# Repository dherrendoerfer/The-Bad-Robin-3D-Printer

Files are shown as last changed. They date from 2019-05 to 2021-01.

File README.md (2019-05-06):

# The Bad Robin 3D Printer
The Bad Robin 3D Printer is an Open-Source 3D Printer project. Its goal is to provide an 
affortable, versatile and robust 3D Printer design.  
It was designed for the use in schools and universities, where the availablility of spare parts are key to the success
of a 3D Printer, and so it was designed to be able to produce its own spare parts. Also a school printer should be easy to store,
so this frame design was chosen to use as little shelf space as possible .  

### Main design features
- It is built-up of only well-established parts that are widely available.
- It features a new single-fan extruder desing for a super-light extruder with print cooling.
- It is parametric: Height, width or length may change, the 3D-Printed parts that make it up always remain the same.
- It is rugged: The base and frame are very strong if the printer ever becomes un-aligned it is very easy to fix.
- It provides superior quality prints: The desing is made to minimise vibrations and wobble making for great prints.
- It can replicate: Even the smallest (250mm) variant can print all the parts for its larger siblings.
- It is affordable: Depending on sourcing, the price does not exceed $250 for the 250mm version. 
- It is expandable: Multicolor or Heated printbed ? Everything is possible.

Licensed under GPL:
## The Bad Robin 3D printer project files
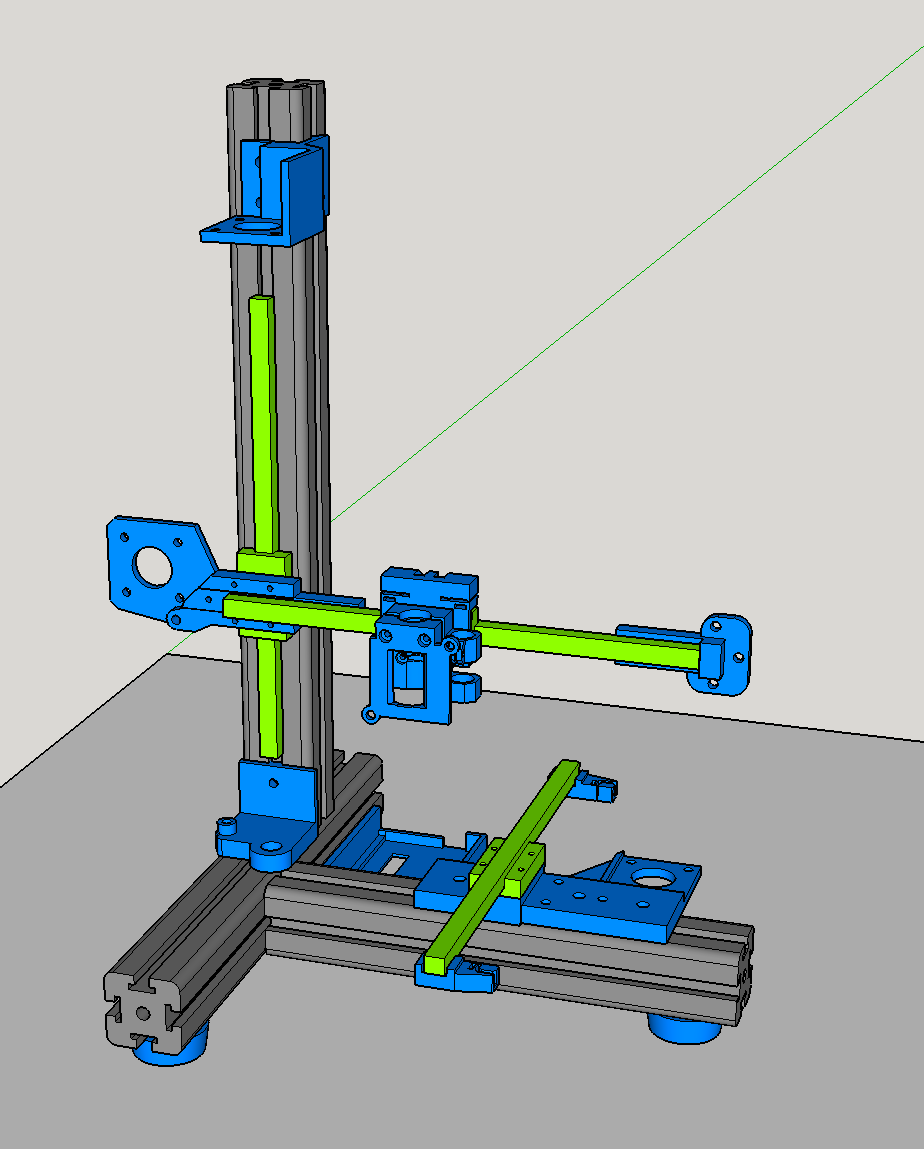
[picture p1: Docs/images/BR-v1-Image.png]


For more information see the Bill-of-materials and the documentation in the Docs directory.

## Videos:
The development of the 3D Printer and its beginnings are documented on my YouTube Channel.  

The general intro video is here:  
https://www.youtube.com/watch?v=5juObRKD8EM&list=PLotvT33qzzfLR7SWEICwr2An6o4muybxc

There is a build video available here:  
https://www.youtube.com/watch?v=sfIAuq82kME&list=PLotvT33qzzfLR7SWEICwr2An6o4muybxc

And don't forget:  
    have FUN!  
D.Herrendoerfer

Donations:  
If you would like to make a donation to keep this project and others going you can do so at:  
https://www.paypal.me/dherrendoerfer  
This helps a lot !

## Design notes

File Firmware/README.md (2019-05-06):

### Firmware files for the Bad Robin 3D printer
This folder includes the required files for building the firmware for the Bad Robin
3D printer. Note that these files may be out-of-sync with the official version of Repetier.

The official Repetier firmware can be found here: https://www.repetier.com/documentation/repetier-firmware/

Repetier is licensed under the GNU GENERAL PUBLIC LICENSE (v3). A copy of the license can be found in the
same directory as this file. Make sure to read and understand it before sharing anything contained here.

The version of Repetier in the Repetier directory contains software addons required for the operation and
safety of the Bad Robin Printer. Do not operate the 3D printer without porting these changes forward.

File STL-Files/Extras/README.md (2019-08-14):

This folder contains things that are strictly speaking not needed for the bare printer, but might help the interrested to get it looking or working neater.

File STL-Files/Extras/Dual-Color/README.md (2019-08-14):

## Multi Meaterial Mod Files
These files are for a modification to support dual material/color print 
Note that the tubes inside the Y-mixer need to be lined with PTFE tube, and the end of the joining (single) tube should be opened up with a drill to help with the insertion of the filament. 
All the connections should be made with locking PTFE clamps, make sure not to overtighten them.

The firmware for the dual color mod and the tool-change scripts are not freely available yet, please contact me for a copy if you can't get it to work yourself. 

###This is still Work-In-Progress

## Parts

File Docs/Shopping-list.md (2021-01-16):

##Shopping list (Date: Feb. 2020):

- ITEM Profile:

https://www.ebay.de/itm/ALU-Profil-Aluprofil-40x40-Nut-8-Aluminium-Profil-AlClipTec/261818937804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

- Bearings:

https://www.ebay.de/itm/20-Kugellager-685-2RS-5-x-11-x-5-mm/251275830725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

- TR8 Nut:

https://www.ebay.de/itm/Trapezgewindemutter-ESKM-8x1-5-rechts-Stahl-Sechskant-SW15L12/273422712592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

or

https://www.ebay.de/itm/Trapezgewindemutter-ESKM-MS-8X1-5-rechts-Rotguss-Sechskant-SW17L15/273700033030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

- TR8 Rod: 

https://www.ebay.de/itm/Prazisions-Trapezgewindespindel-RPTS-TR-8X1-5-rechts-C35-C45-50cm/273177877971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

- Profile Nuts (8mm) 

* You need M3, M5, and M6

https://www.ebay.de/itm/Aluprofil-Profil-10x-Nutensteine-T-Nut-M5-Nut-8/380187272689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

https://www.ebay.de/itm/Aluprofil-Profil-10x-Nutensteine-mit-Kugel-Nut-8/262643806083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

* This type for the M3:

https://www.ebay.de/itm/Nutensteine-schwer-fur-40er-45er-Aluprofile-Stahl-Nut-8-10-M3-M4-M5-M6-M8/132371894755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

- Linear Rail:

https://www.amazon.de/gp/product/B07LDBNVTW  

- Proximity Switch:

https://www.amazon.de/gp/product/B071ZQ6VV6/ref=oh_aui_detailpage_o01_s00?ie=UTF8&psc=1

- Hot-End:

https://www.amazon.de/YOTINO-Extruder-Drucker-Makerbot-Messing/dp/B078SLDBY3/ref=sr_1_5_sspa

- Fan:

https://www.amazon.de/gp/product/B06XZR6VQV/ref=oh_aui_detailpage_o03_s00?ie=UTF8&psc=1

- Extruder Driver: ( Order the 3-Pieces set !)

https://www.amazon.de/TEVO-Titan-Extruder-Komplettpaket-17-Schrittmotor-Bowdenzug-Befestigungsschellen/dp/B073YMY6CP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

- Steppers:

https://www.ebay.de/itm/Longs-Motor-stepping-motor-17HS4401N-nema17-57oz-for-3D-Printer-Reprap-DE-Ship/202105774039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

- RAMPS Kit:

http://bit.ly/3rPzlYX
or (if available):
https://www.amazon.de/Controller-Schrittmotor-Treiber-Heatsink-Grafik-Smart-Display-Controller-3D-Drucker/dp/B01NCZ09Q5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

- Belt & Pulley

https://www.amazon.de/MOHOO-Zahnriemen-Riemenscheibe-Bohrung-Drucker/dp/B01AU3LRRG/ref=sr_1_2_sspa

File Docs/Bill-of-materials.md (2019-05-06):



### All files and information provided here is licensed under the GNU PUBLIC LICENSE 
Make sure you understand the license requirements and implications before moving on.

### Design decision:
The Z-Axis can be held in place by a 3D-printed part and a ball-bearing ball, or a different 3D-printed part and a bearing. For this mounting method the threaded rod needs to be machined to fit the bearing. (Items that this influences are marked with *)

### Bill of materials

- You need each and every stl file printed once, the feet 3 times.
- You need T-Nuts with M3, M5, and M6 screws in various sizes and lengths.
- You need a drill-press to drill two holes

Please also consult the file:
https://github.com/dherrendoerfer/The-Bad-Robin-3D-Printer/blob/master/Docs/Shopping-list.md 
for hints on what to get.

#### You need to source:
- 3x MGN12H linear rails with 250mm length 
- 1x ITEM 40mm aluminium profile 400mm long
- 1x ITEM 40mm aluminium profile 300mm long
- 1x ITEM 40mm aluminium profile 250mm long
- 3x Stepper motors NEMA17 bipolar
- 1x Threaded rod TR8 315mm long (320mm if using a bearing* for the Z-Axis)
- 1x Threaded rod nut TR8
- 1x Steel ball bearing ball with 3.5 to 4.5mm diameter (or 1x bearing* 5x11x5mm)
- 1x Shaft coupler 5mm to 8mm
- 1x Kit Arduino+Ramps+Graphic-Display+Stepsticks
- 1x Tevo Titan extruder driver kit with stepper
- 1x V6 J-Type Hotend with sensor and heater
- 2x Flat pushbutton end-switches
- 2x Timing belts with 2x driver (T2)
- 1x Turbine Fan
- 1x Inductive proximity switch NPN, NO(normally open)
- 1x Rod-Connection 5mm to 8mm
- 10x Bearings 5x11x5mm
- M6 threaded rod 440mm and 290mm long

### Print settings for the 3D printed parts
* With 0.4mm nozzle diameter and PLA use 30% infill and 3 shell layers at least
* With 0.3mm nozzle diameter and PLA use 35% infill and 4 shell layers at least
* Use brim
* Use higher temp and low print speed for good layer-bond.
* Use a drill to bring each hole to required bore diameter
* Make sure to clean up all the edges of the prints before assembly.

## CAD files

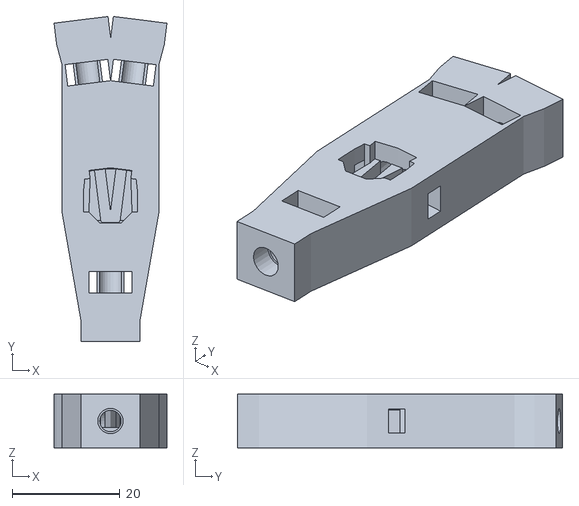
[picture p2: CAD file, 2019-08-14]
STL-Files/Extras/Dual-Color/Rob-Multi-Extruder-Mixer7.stl
21.0 x 60.3 x 10.0

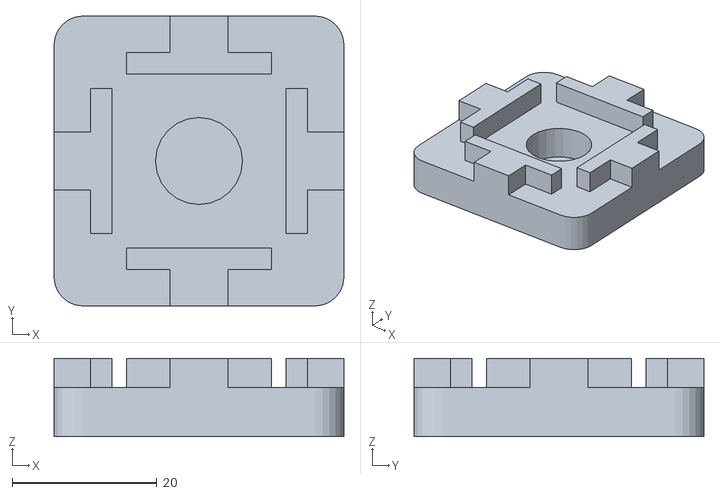
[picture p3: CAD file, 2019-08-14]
STL-Files/Extras/Item40Plug.stl
40.0 x 40.0 x 10.8

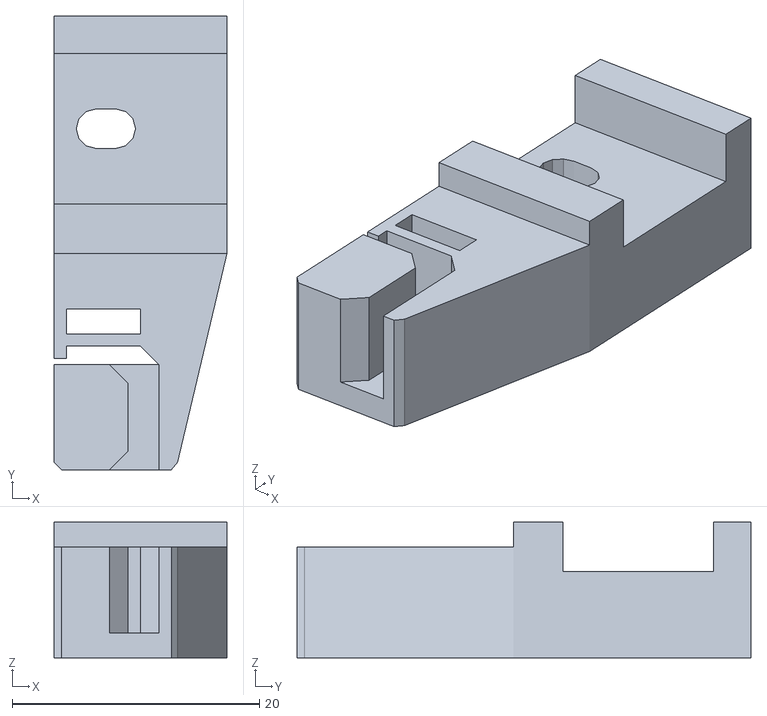
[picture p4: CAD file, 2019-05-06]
STL-Files/BR-v1-Y_Belt_Back.stl
14.0 x 36.7 x 11.0

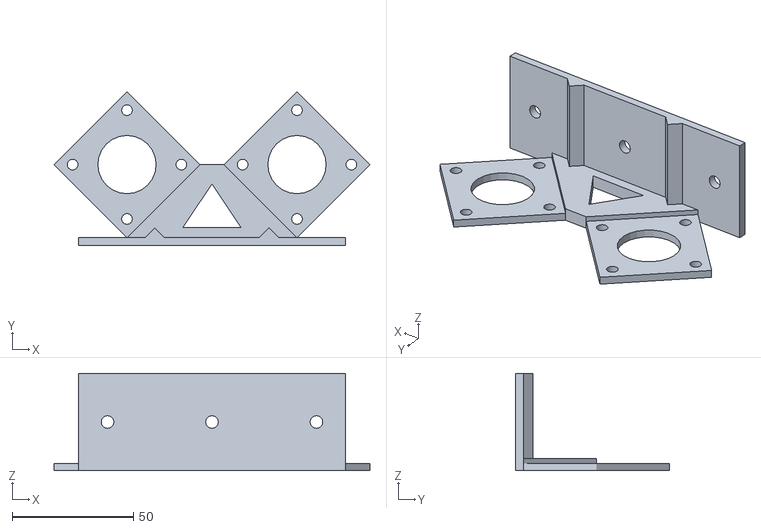
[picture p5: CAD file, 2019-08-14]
STL-Files/Extras/Dual-Color/DualExtruderDriverMount.stl
130.1 x 63.3 x 40.0

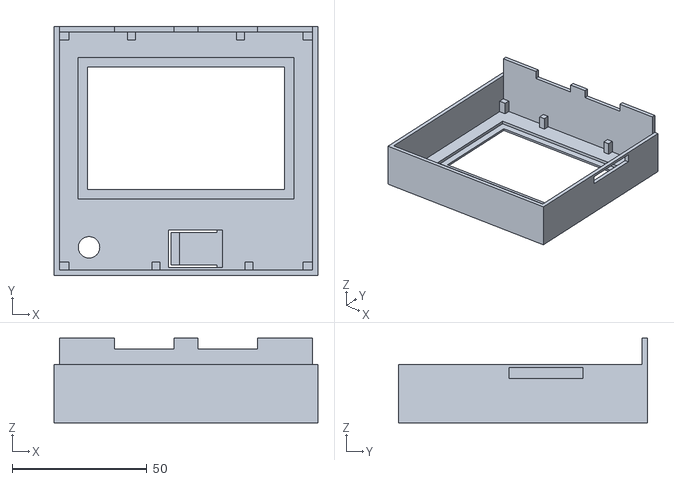
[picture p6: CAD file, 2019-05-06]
STL-Files/BR-v1-Display_Holder.stl
98.0 x 92.5 x 31.5

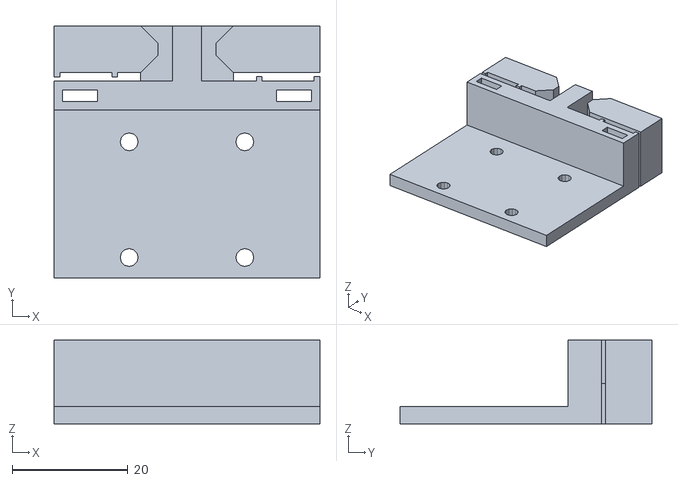
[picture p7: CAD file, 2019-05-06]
STL-Files/BR-v1-X_Belt_Mount.stl
46.0 x 43.5 x 14.5

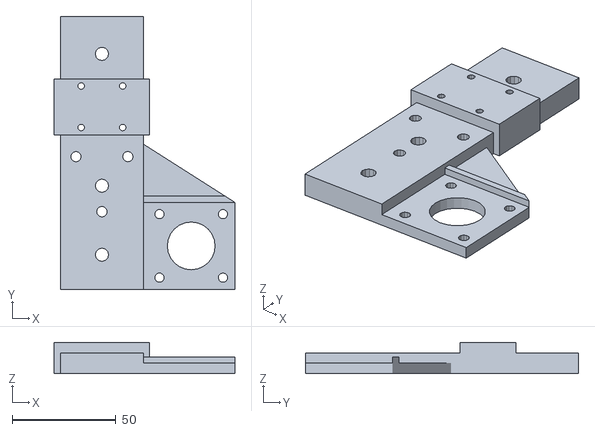
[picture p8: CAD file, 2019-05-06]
STL-Files/BR-v1-Y_Motor_Mount.stl
87.0 x 131.5 x 15.0

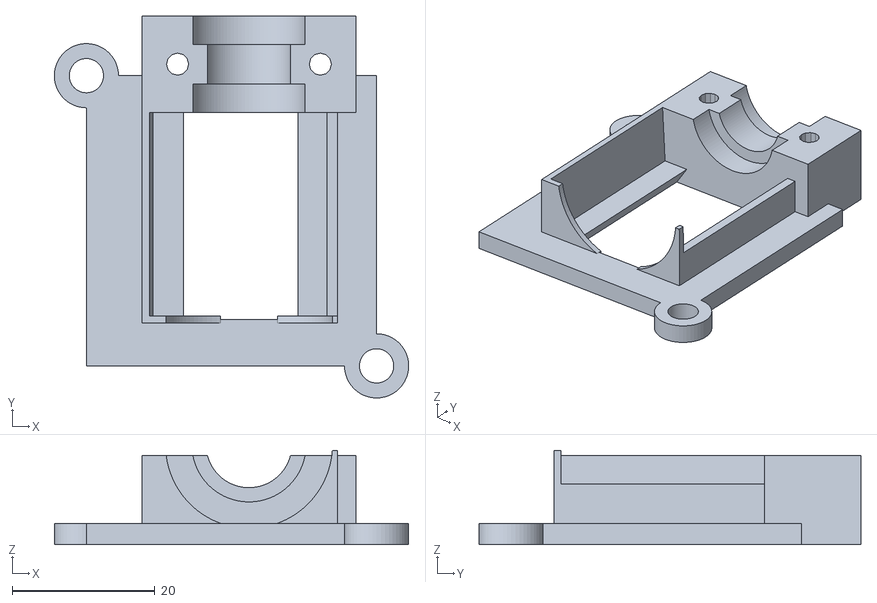
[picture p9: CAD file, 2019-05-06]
STL-Files/BR-v1-Hotend_Mount-B.stl
49.7 x 53.5 x 13.2

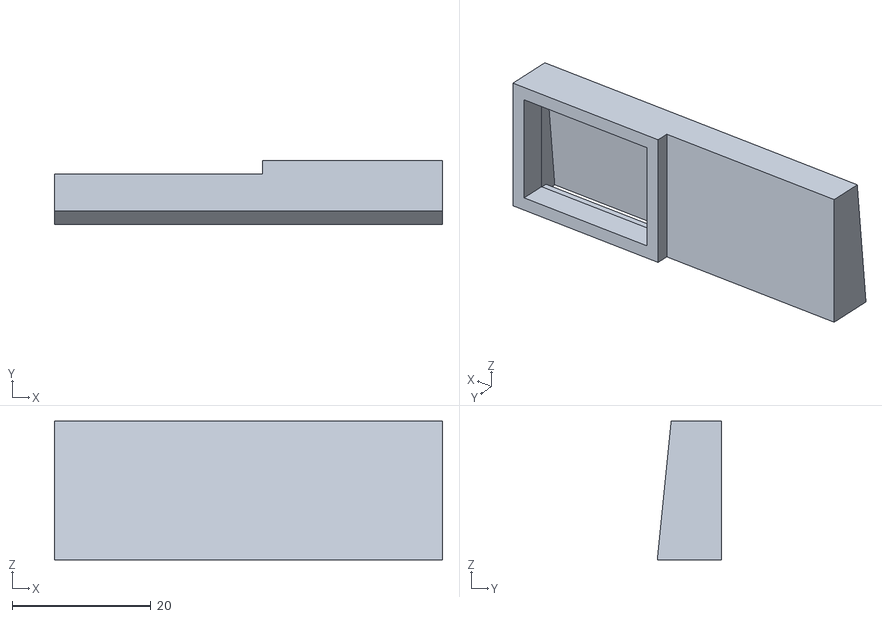
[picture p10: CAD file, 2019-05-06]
STL-Files/BR-v1-Fan_Shroud.stl
56.0 x 9.30 x 20.0

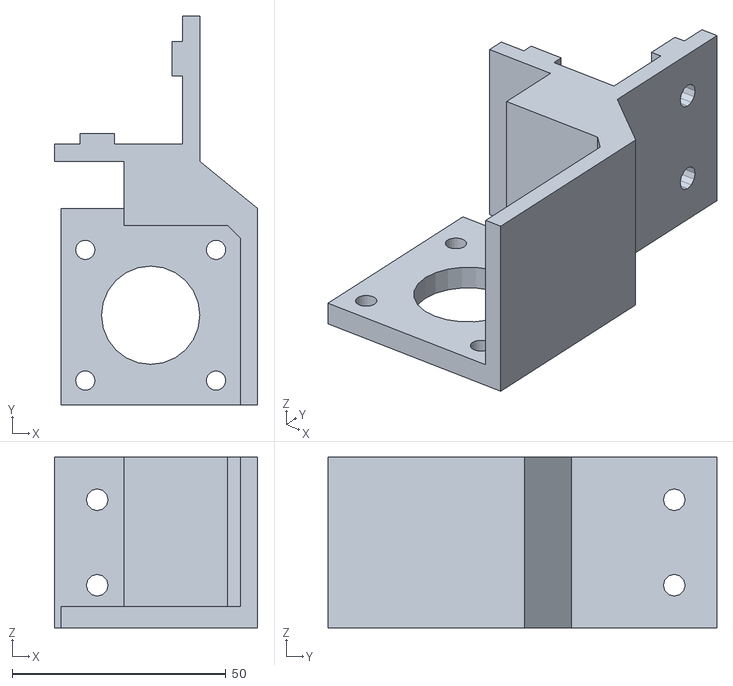
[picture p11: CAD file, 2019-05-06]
STL-Files/BR-v1-Z_Motor_Mount.stl
47.5 x 91.0 x 40.0

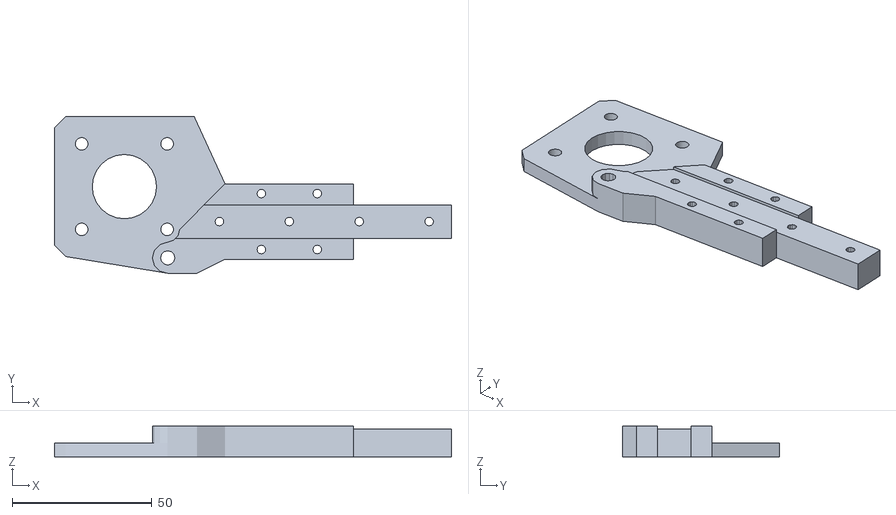
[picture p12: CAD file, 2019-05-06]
STL-Files/BR-v1-X_Motor_Mount.stl
142.0 x 56.0 x 11.0

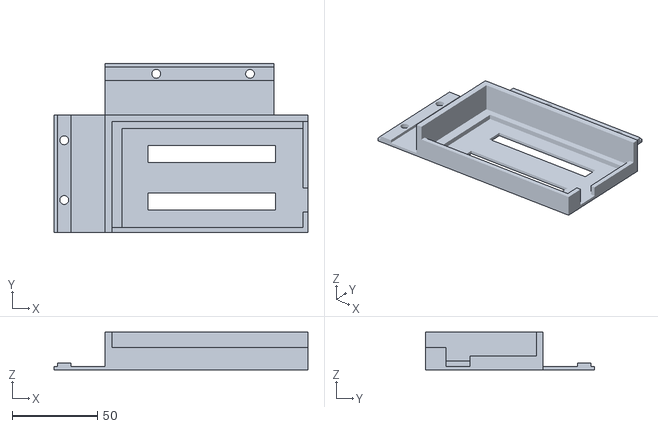
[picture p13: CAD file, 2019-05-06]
STL-Files/BR-v1-RAMPS_Holder.stl
149.0 x 99.0 x 22.0

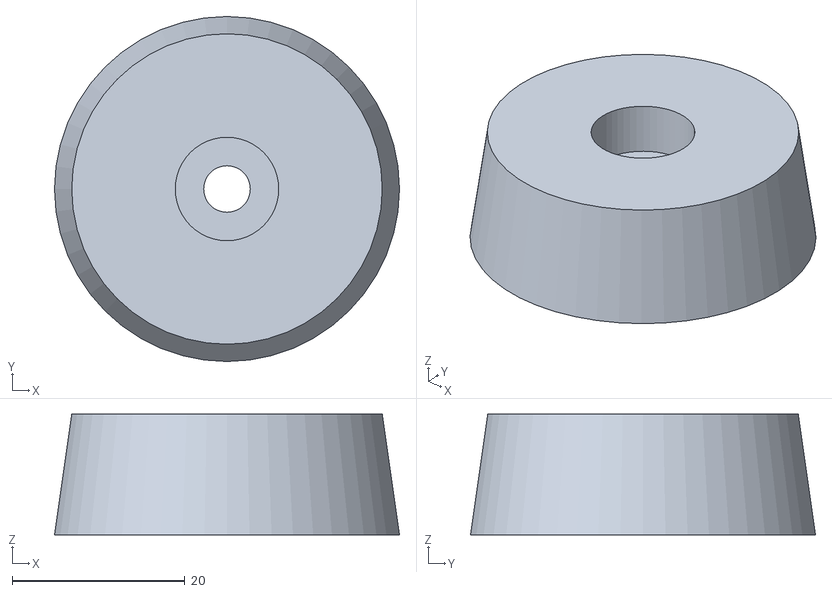
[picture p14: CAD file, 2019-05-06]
STL-Files/BR-v1-Foot.stl
40.0 x 40.0 x 14.0

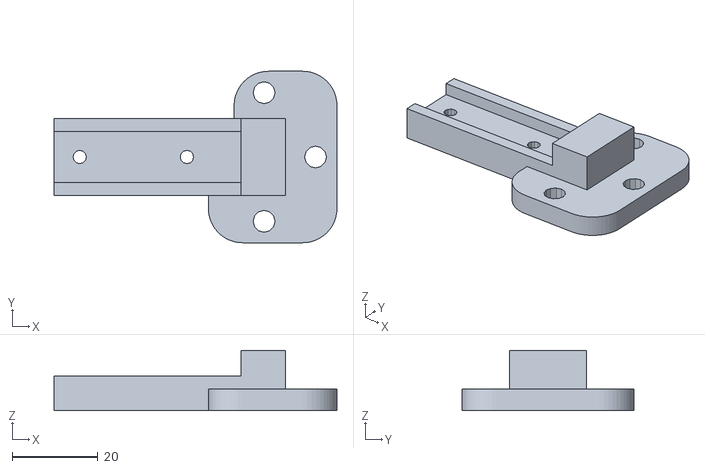
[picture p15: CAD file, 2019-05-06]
STL-Files/BR-v1-X_Idler.stl
66.0 x 40.0 x 14.0

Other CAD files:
STL-Files/BR-v1-Hotend_Mount-A.stl
STL-Files/BR-v1-Y_Belt_Front.stl
STL-Files/BR-v1-Z_Idler_nobearing.stl
STL-Files/BR-v1.stl
STL-Files/BR-v1-Z_Idler.stl
STL-Files/BR-v1-Z_Nut_Holder-15mm.stl
STL-Files/BR-v1-Z_Nut_Holder-A.stl
STL-Files/BR-v1-Z_Nut_Holder-B.stl

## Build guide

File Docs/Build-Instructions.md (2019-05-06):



### Build video:
The steps in this manual match up with this video:  
https://www.youtube.com/watch?v=sfIAuq82kME&list=PLotvT33qzzfLR7SWEICwr2An6o4muybxc

### Build instructions:

## Part 1: Build the frame
# Prepare the Frame parts

Drill the holes to join the ITEM profiles.

The frame consists of three profiles, two of them need to be joined to the
third by drilling a hole for each joining part in it.

For the 250mm printer, the holes must be drilled in one axis at 130mm and the second
hole must be drilled at 200mm on the other axis. The bore diameter should be 6mm.

Take care, and make sure the holes are in the middle of the rod and at a perfect 90
degree angle. Use a drill press if available.

The Frame parts should be cleaned of any metal shavings or sharp edges.

# Assemble the frame

Using two 6mm threaded rods mount the two ITEM profiles to the profile with the 
two holes. Make sure that all parts are perfectly in line, and at 90 degree angles
to the center profile.

Tighten down the threaded rods well with M6 nuts. You can use glue on the profiles,
but you do not need to. One nut should be recessed inside the profile, the other open
at the profile end.

Finally add the feet using the 3D-printed parts and 20mm M5 screws and M5 T-nuts.

## Part 2: Add the Z-axis idler
# Choose your idler

There are two options available here, but one requires machining the threaded rod one
a lathe, creating a step with 5mm diameter one one side. 

The other idler just needs a small metal ball from a ball bearing to be inserted into its
center opening, and the threaded rod will rotate on that.

# Mounting the idler

Use the selected 3D-printed part, fit it onto the profile with a M5 T-nut and a 12mm M5
screw.

## Part 3: Mount the Arduino cradle

Use four M5 T-nuts and 12mm M5 screws to attach the cradle to the bottom of the frame
parallel to the short end of the X and Y-profile.

## Part 4: Assembling the Y-axis

Get the Y-axis motor mount 3D-printed part.

Cut two M5 hex head screws to 22mm. Put four 15mm M3 screws into the 3mm holes, make sure
screws fit well into the recess. Place the two 22mm M5 into the holes closest to the rail.
Screw a M5 nut onto each M5 screw, tighten that well. Add two 11x5x5mm bearings to each
screw, and fix them down with a M5 nut.

Screw the M3 screws carefully into the rail block, using a 1,3,2,4 pattern and fix with
reasonable force. Make sure that the rail is parallel to the bottom.

Add three 20mm M6, large washers, and M6 T-nuts to the part, to fix it to the profile.

Slide the Y-axis part onto the X-axis profile and tighten lightly.

Add the Y-axis belt holders to the end of the rail using 30mm M3 screws and M3 nuts

## Part 5: Assembling the X-axis

Get the X-axis motor mount 3D-printed part. Make sure the rail fits the grove in the 
part perfectly.

Place the rail over the 3D-printed part so that the 3mm hole in the grove closest to
the stepper position is not covered by the rail.

Place a 30mm M3 screw into the hole with the recess from back to the front where the
rail is. Add a M3 washer and a M3 nut onto the rail side and tighten well.

Repeat this for the next hole.

The third screw is screwed from the rail to the plastic. Use a 16mm M3 screw inserted into
the recess of the rail with a M3 nut on the plastic. Tighten well.

Get the linear rail for the Z-axis and screw the 3D-printed part with four 16mm M3 screws
into the rail block using 1,3,2,4 pattern and tighten well.

Optional: you may want to thread cable ties through the last holes and the back edge of
the rail to keep the block from sliding of the rail while building the printer.

Now slide the rail onto the Z-axis profile using two 16mm M3 screws and M3 T-nuts. Use the
second hole fron the top and bottom. Just tighten lightly, keep about 5cm distance to the 
Z-axis idler.

Then slide the Z-axis motor mount onto the top of the Z-axis profile using four 
12mm M5 screws and M5 T-nuts. Also tighten lightly. 

Fix the X-axis belt holder to the X-axis sliding block with a single M3 screw. 

Add the X-axis idler by screwing it to the rail using two 16mm M3 screws and M3 nuts.
Into the top and bottom hole of the idler place two 20mm M5 screws. On the rail side
add a 10x5mm washer, two 11x5x5mm bearings snd fix them with a M5 nut. Tighten well.
Insert a third 20mm M5 screw into the remaining hole and fix with a M5 nut.

## Part 6: Assembling the Z-axis

Assemble the Z-axis decoupler by fitting the TR8 hex nut guide over the TR8 nut making
sure that the guide sits on the nut tightly. Insert a 18mm M3 screw into the coupler
and into the guide and fix with a M3 nut.

Install the 11x5x5mm bearing into the Z-axis idler, or insert the ball bearing ball into 
the rod hole (depending on the type of idler you are using). Make sure that the lower edge
facing the profile is very clean, so the idler sits snug on the lower profile and the 
bearing to the threaded rod has no play.

Place the decoupler on the rod and insert the rod onto the idler. Slip the decoupler onto
two screws protruding fron the X-axis rail, the decouplers screw should be on the side of
the stepper.

## Part 7: Add the extruder mount

The extruder mount is is attached to the X-axis using two 10mm M3 screws at the lower two 
holes. Before mounting that, add a 10mm M3 screw and nut to the clamp of the Z-axis level
sensor. 

## Part 8: Mount the stepper motors

Mount the three NEMA17 steppers into their positions using 8mm or 10mm M3 screws and washers.
Don't forget to add the 5mm to 8mm coupler to the Z-axis rod and stepper. The Z-axis 
threaded rod and the stepper shaft should not be touching inside the coupler, but have
about 2mm of distance. 

## Part 9: Add the last X-axis belt idler

Below the X-axis stepper on the motor mount part, there is a 5mm hole, where the last belt 
idler needs to go. Put a 30mm M5 hex-head screw into this hole, add two M5 washers, then
two 11x5x5mm bearings and finally a M5 nut. tighten this well.

## Part 10: Fit the belts

Add a pulley to the X and Y-axis steppers. 

Start with the X-axis and thread the belt into the belt holder on the side facing the 
idler. The toothed side of the belt must be facing up, so the belt touches the bearings 
with the smooth side. Thread the belt around to the stepper, flipping it over between the
left and right idler on the bottom. Thread the belt into the side of the belt holder facing 
the stepper with the toothed side to the bottom. Tighten until there is no play in the 
printer carriage when the stepper is not turning. There does not need to be a lot of 
tension on the belt.

Add the belt to the Y-axis by mounting the belt to the holders and threading it around
the pulley via the bearings. Also tighten lightly to the point where there is no slack
in the belt.

## Part 11: Mount the level probe

Insert the level probe into the mount on the extruder mount assembly make sure it is able
move all the way down. Tighten slightly, make sure it sits snug in its place.

## Part 12: Prepare the extruder

Verify that the extruder has a PTFE liner inside the throat piece. Make sure that the 
temperature probe is fastened securely inside the block and that the heater does not
stick put of the front of the heater block by more than 2mm.

Choose a nozzle size. (Anything from 0.2 to 0.5mm should work well.)

Check that the nozzle is securely screwed into the heating block.

## Part 13: Mount the extruder

Place the extruder against the extruder mount, check that the cables exit to the back and
that the heating block is parallel to the mount so the heater cannot touch the fan holder.

Mount the extruder to the carriage by screwing two 30mm M3 screws trough the fan holder 
into the extruder mount, thereby clamping the extruder to the carriage and the mount.

Make sure that the fan holder is parallel to the mount. 

Check that the extruder is fastened securely.

## Part 14: Prepare the wiring 

Make sure that all cables for steppers, fan, switches, sensor and power supply have enough
length to reach the RAMPS board. 

For the switches you need to manufacture two sets of end switches, one should have about 
70cm cable length, the other about 20cm.

The cable for the fan should, in total, be about 70cm in length add a plug close to the 
fan to make replacing it easier.

The cables from the extruder and temp sensor should be long enough, if not: extend them to 
about 70cm.

The cable for the X-axis stepper should be about 70cm long, the Y-axis stepper needs just 
about 25cm of cable.

Also, make a power plug for the RAMPS board.

## Part 15: Add the Arduino and RAMPS boards 

Optional: Remove the power plug from the Arduino, in case it touches on the power connector
solder spots of the ramps too much.

Join the Arduino and RAMPS board.

Using thick double-sided tape stick the Arduino into the cradle,and make sure that it is
fastened well. The USB plug should go into the recess on the cradle and line up with that.

## Part 16: Mount the home switches

# X-axis
The X-axis home switch is placed on the small block on the extruder mount, and glued in
place there using hot glue. It should engage when the extruder is moved all the way into
the left position.

# Y-axis
The Y-axis home switched needs to be glued onto the Y-axis motor mount, so it engages when
the screw from the Y-axis belt holder comes closest to the front of the mount. Glue it in
place with hot glue and check that it engages when the Y-axis homes.

## Part 17: Add the extruder driver

Assemble the Tevo Titan extruder.

Enlarge the two mounting holes on the extruder driver mount to 5mm and fix the extruder
driver with two 12mm M5 screws and M5 T-nuts to the Z-axis profile. Keep about 13cm 
distance to the top of the profile.

## Part 18: Mount the PTFE feeder tube

Cut about 36cm PTFE tube (250mm model).

Push the PTFE feeder tube all the way into the extruder and the extruder driver.

## Part 19: Managing cables

Add two cable ties to the X-axis belt holder on the side of the X-axis idler.
With one of those cable ties fix down the belt to the holder, with the second cable
tie fix the extruder heater, and temperature sensor cable to the carriage, creating a 
cable loop large enough that the X-axis can travel all the way to the left and right. 
Check that the cables do not touch the rail or the idler.

Fix the fan to the fan mount with two 20mm M4 screws and M4 nuts.

Using a cable tie attach all cables from the X-axis carriage to the PTFE tube and route
all cables along the PTFE tube to the extruder driver.

Beyond the driver to the RAMPS board add the X and Z-axis stepper and the extruder driver 
stepper cable to the cable bundle and route all those down to the RAMPS board along the 
back of the Z-axis profile.

Use cable wrap to fix the cables together.

## Part 20: Adding connectors and firmware

Cut the cables to optimal length and add female connectors to the stepper and sensor 
cables.

Download and transfer the Repetier firmware to the Arduino. Use the firmware from this repo,
as the construction of the extruder requires a modified version of the Repetier firmware.

## Part 21: Connect the display unit

Mount the display unit into the display case, make sure that the reset switch and the 
SD-card are accessible and work. 

Add the display daughter board to the RAMPS board and connect it to the display with the
cables.

Add the stepper driver modules (X,Y,Z,E0) to the RAMPS board.

Optional: Fix the cables to the frame using hot-glue or double-sided tape.

## Part 22: Connect electronics to controller

Connect the home switches
- X home switch to Xmin pin.
- Y home switch to Ymin pin.
- Z level probe (output) to Zmax

Connect the positive and negative lead of the level probe (brown+,blue-) to the aux 12 
pins between the X stepper driver and the fuses. 

Connect the steppers (pins left to right)
- X-axis stepper to X (order: black,green,blue.red)
- Y-axis stepper to Y (order: black,green,blue.red)
- Z-axis stepper to Z (order: red,blue,green,black)
- Extruder driver stepper to E0 (order: black,green,blue.red)

Connect the temp sensor to T0

Connect the extruder heater to D10

Connect the extruder fan to D9, watch the polarity !

## Part 23: Test motors and switches

# 1st test
Connect the printer to power.

The display should come alive and the fan should spin up and run at high intensity for
about 15 seconds then the fan should ramp down to a low RPM but not stop.

# 2nd test
Using the display move each stepper using manual movement (fast) for 1mm.

The steppers should move in the right direction, they should not be emitting any noise
or vibrate. if yes, lower the current on the stepper.

# 3rd test
Heat the extruder to 170 degrees

The extruder should warm up. Abort the test once it passes 60 degrees Celsius.

# 4th test
Try to home X and Y-axis

The printer should move the axis to the home position

# 5th test
Navigate to the move Z-axis fast menu.

Place a metal object on the bottom of the Z-axis level sensor. The LED at the top
of the sensor should light up and the status for the end-stop should change on the 
display.

## Part 24: Finishing up

Mount the build platform to the Y-axis rail of the printer.

Glue the fan shroud to the fan outlet, making sure it is 1mm higher than the nozzle and
parallel to the table.

Measure that all axis are perpendicular to each other.

Measure that the table and the Z-axis rail are perfectly parallel.

Manually set the Z-axis to touch the table.

Push the level sensor down until it too touches the Table then turn the sensor one 
half turn counterclockwise. Perform a Z-axis homing. Adjust the height of the probe
by turning it until the Z-axis homes perfectly to touch the platform just barely.

Do a test print (Remember to add a G32 command on the last line to the init g-code for 
auto bed-leveling)
During the test print check the current to the extruder driver, keep an eye on the 
extruder temperature.

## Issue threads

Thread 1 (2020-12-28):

Parametric design

sam-d, 2020-12-28:
The readme states that the design is parametric. Could you please provide more information on the design constraints?

I would like to know how the length of the rails in each axis affect the print volume. Also why is the design with 250mm rails considered minimal? Is there any contraint that would preclude using smaller rails?

I am looking to build a printer with a 215x215mm bed size and perhaps restrain the Z axis to 100mm as I rarely print tall pieces. What dimensions of extrusions and rails would I need?

dherrendoerfer, 2020-12-28:
Hello,

The design does not require any changes in the 3D prints no matter what size you use for the rails. (between 250 and 450mm) The parts themselves are not parametric.
The limit of 250mm rails only refers to its ability to print all the parts for another Bad Robin, you can of course also go smaller, in fact it's not even required for the height.
250mm rails on X and Y axis give you a useable print area of 155x160mm. On the Z axis it's about 170mm (with room to spare)

The rails and extrusions are for 250mm, add the same amount you add for the rail to the extrusion, add half of the Y change to the drill hole positions on the base extrusion.

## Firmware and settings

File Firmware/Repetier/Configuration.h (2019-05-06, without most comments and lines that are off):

#define CONFIGURATION_H
#define NUM_EXTRUDER 1
#define MOTHERBOARD 33
#include "pins.h"
#undef FAN_PIN
#define FAN_PIN HEATER_2_PIN
#undef FAN_BOARD_PIN
#define FAN_BOARD_PIN -1
#define BOARD_FAN_SPEED 255
#define FAN_THERMO_PIN -1
#define FAN_THERMO_MIN_PWM 128
#define FAN_THERMO_MAX_PWM 255
#define FAN_THERMO_MIN_TEMP 45
#define FAN_THERMO_MAX_TEMP 60
#define FAN_THERMO_THERMISTOR_PIN -1
#define FAN_THERMO_THERMISTOR_TYPE 1
#undef Z_MIN_PIN
#define Z_MIN_PIN ORIG_Z_MAX_PIN
#define BLUETOOTH_SERIAL  -1
#define BLUETOOTH_BAUD  115200
#define MIXING_EXTRUDER 0
#define DRIVE_SYSTEM 0
#define XAXIS_STEPS_PER_MM 80
#define YAXIS_STEPS_PER_MM 80
#define ZAXIS_STEPS_PER_MM 2133.33
#define EXTRUDER_FAN_COOL_TEMP 50
#define PDM_FOR_EXTRUDER 0
#define PDM_FOR_COOLER 0
#define DECOUPLING_TEST_MAX_HOLD_VARIANCE 20
#define DECOUPLING_TEST_MIN_TEMP_RISE 1
#define KILL_IF_SENSOR_DEFECT 0
#define RETRACT_ON_PAUSE 2
#define PAUSE_START_COMMANDS ""
#define PAUSE_END_COMMANDS ""
#define SHARED_EXTRUDER_HEATER 0
#define EXT0_X_OFFSET 0
#define EXT0_Y_OFFSET 0
#define EXT0_Z_OFFSET 0
#define EXT0_STEPS_PER_MM 376.14
#define EXT0_TEMPSENSOR_TYPE 1
#define EXT0_TEMPSENSOR_PIN TEMP_0_PIN
#define EXT0_HEATER_PIN HEATER_0_PIN
#define EXT0_STEP_PIN ORIG_E0_STEP_PIN
#define EXT0_DIR_PIN ORIG_E0_DIR_PIN
#define EXT0_INVERSE 0
#define EXT0_ENABLE_PIN ORIG_E0_ENABLE_PIN
#define EXT0_ENABLE_ON 0
#define EXT0_MIRROR_STEPPER 0
#define EXT0_STEP2_PIN ORIG_E0_STEP_PIN
#define EXT0_DIR2_PIN ORIG_E0_DIR_PIN
#define EXT0_INVERSE2 0
#define EXT0_ENABLE2_PIN ORIG_E0_ENABLE_PIN
#define EXT0_MAX_FEEDRATE 50
#define EXT0_MAX_START_FEEDRATE 20
#define EXT0_MAX_ACCELERATION 5000
#define EXT0_HEAT_MANAGER 3
#define EXT0_WATCHPERIOD 1
#define EXT0_PID_INTEGRAL_DRIVE_MAX 230
#define EXT0_PID_INTEGRAL_DRIVE_MIN 40
#define EXT0_PID_PGAIN_OR_DEAD_TIME 7
#define EXT0_PID_I 2
#define EXT0_PID_D 40
#define EXT0_PID_MAX 255
#define EXT0_ADVANCE_K 0
#define EXT0_ADVANCE_L 0
#define EXT0_ADVANCE_BACKLASH_STEPS 0
#define EXT0_WAIT_RETRACT_TEMP 150
#define EXT0_WAIT_RETRACT_UNITS 0
#define EXT0_SELECT_COMMANDS ""
#define EXT0_DESELECT_COMMANDS ""
#define EXT0_EXTRUDER_COOLER_PIN -1
#define EXT0_EXTRUDER_COOLER_SPEED 255
#define EXT0_DECOUPLE_TEST_PERIOD 12000
#define EXT0_JAM_PIN -1
#define EXT0_JAM_PULLUP 0
#define FEATURE_RETRACTION 1
#define AUTORETRACT_ENABLED 0
#define RETRACTION_LENGTH 3
#define RETRACTION_LONG_LENGTH 13
#define RETRACTION_SPEED 40
#define RETRACTION_Z_LIFT 0
#define RETRACTION_UNDO_EXTRA_LENGTH 0
#define RETRACTION_UNDO_EXTRA_LONG_LENGTH 0
#define RETRACTION_UNDO_SPEED 20
#define FILAMENTCHANGE_X_POS 0
#define FILAMENTCHANGE_Y_POS 0
#define FILAMENTCHANGE_Z_ADD  2
#define FILAMENTCHANGE_REHOME 1
#define FILAMENTCHANGE_SHORTRETRACT 5
#define FILAMENTCHANGE_LONGRETRACT 50
#define JAM_STEPS 220
#define JAM_SLOWDOWN_STEPS 320
#define JAM_SLOWDOWN_TO 70
#define JAM_ERROR_STEPS 500
#define JAM_MIN_STEPS 10
#define JAM_ACTION 1
#define RETRACT_DURING_HEATUP true
#define PID_CONTROL_RANGE 20
#define SKIP_M109_IF_WITHIN 2
#define SCALE_PID_TO_MAX 0
#define TEMP_HYSTERESIS 0
#define EXTRUDE_MAXLENGTH 160
#define NUM_TEMPS_USERTHERMISTOR0 0
#define USER_THERMISTORTABLE0 {}
#define NUM_TEMPS_USERTHERMISTOR1 0
#define USER_THERMISTORTABLE1 {}
#define NUM_TEMPS_USERTHERMISTOR2 0
#define USER_THERMISTORTABLE2 {}
#define GENERIC_THERM_VREF 5
#define GENERIC_THERM_NUM_ENTRIES 33
#define HEATER_PWM_SPEED 0
#define HAVE_HEATED_BED 0
#define HEATED_BED_MAX_TEMP 120
#define SKIP_M190_IF_WITHIN 3
#define HEATED_BED_SENSOR_TYPE 1
#define HEATED_BED_SENSOR_PIN TEMP_1_PIN
#define HEATED_BED_HEATER_PIN HEATER_1_PIN
#define HEATED_BED_SET_INTERVAL 5000
#define HEATED_BED_HEAT_MANAGER 0
#define HEATED_BED_PID_INTEGRAL_DRIVE_MAX 255
#define HEATED_BED_PID_INTEGRAL_DRIVE_MIN 80
#define HEATED_BED_PID_PGAIN_OR_DEAD_TIME   196
#define HEATED_BED_PID_IGAIN   33
#define HEATED_BED_PID_DGAIN 290
#define HEATED_BED_PID_MAX 255
#define HEATED_BED_DECOUPLE_TEST_PERIOD 300000
#define MIN_EXTRUDER_TEMP 150
#define MAXTEMP 275
#define MIN_DEFECT_TEMPERATURE -10
#define MAX_DEFECT_TEMPERATURE 290
#define SUPPORT_LASER 0
#define LASER_PIN -1
#define LASER_ON_HIGH 1
#define SUPPORT_CNC 0
#define CNC_WAIT_ON_ENABLE 300
#define CNC_WAIT_ON_DISABLE 0
#define CNC_ENABLE_PIN -1
#define CNC_ENABLE_WITH 1
#define CNC_DIRECTION_PIN -1
#define CNC_DIRECTION_CW 1
#define DEFAULT_PRINTER_MODE 0
#define ENDSTOP_PULLUP_X_MIN true
#define ENDSTOP_X_MIN_INVERTING true
#define MIN_HARDWARE_ENDSTOP_X true
#define ENDSTOP_PULLUP_Y_MIN true
#define ENDSTOP_Y_MIN_INVERTING true
#define MIN_HARDWARE_ENDSTOP_Y true
#define ENDSTOP_PULLUP_Z_MIN true
#define ENDSTOP_Z_MIN_INVERTING true
#define MIN_HARDWARE_ENDSTOP_Z true
#define ENDSTOP_PULLUP_X_MAX true
#define ENDSTOP_X_MAX_INVERTING false
#define MAX_HARDWARE_ENDSTOP_X false
#define ENDSTOP_PULLUP_Y_MAX true
#define ENDSTOP_Y_MAX_INVERTING false
#define MAX_HARDWARE_ENDSTOP_Y false
#define ENDSTOP_PULLUP_Z_MAX true
#define ENDSTOP_Z_MAX_INVERTING false
#define MAX_HARDWARE_ENDSTOP_Z false
#define max_software_endstop_r true
#define min_software_endstop_x false
#define min_software_endstop_y false
#define min_software_endstop_z false
#define max_software_endstop_x true
#define max_software_endstop_y true
#define max_software_endstop_z true
#define ENDSTOP_X_BACK_MOVE 5
#define ENDSTOP_Y_BACK_MOVE 5
#define ENDSTOP_Z_BACK_MOVE 2
#define ENDSTOP_X_RETEST_REDUCTION_FACTOR 3
#define ENDSTOP_Y_RETEST_REDUCTION_FACTOR 3
#define ENDSTOP_Z_RETEST_REDUCTION_FACTOR 3
#define ENDSTOP_X_BACK_ON_HOME 1
#define ENDSTOP_Y_BACK_ON_HOME 1
#define ENDSTOP_Z_BACK_ON_HOME 0
#define ALWAYS_CHECK_ENDSTOPS 0
#define X_ENABLE_ON 0
#define Y_ENABLE_ON 0
#define Z_ENABLE_ON 0
#define DISABLE_X 0
#define DISABLE_Y 0
#define DISABLE_Z 0
#define DISABLE_E 0
#define INVERT_X_DIR 0
#define INVERT_Y_DIR 0
#define INVERT_Z_DIR 0
#define X_HOME_DIR -1
#define Y_HOME_DIR -1
#define Z_HOME_DIR -1
#define X_MAX_LENGTH 155
#define Y_MAX_LENGTH 167
#define Z_MAX_LENGTH 180
#define X_MIN_POS 0
#define Y_MIN_POS 0
#define Z_MIN_POS 0
#define DISTORTION_CORRECTION 0
#define DISTORTION_CORRECTION_POINTS 5
#define DISTORTION_CORRECTION_R 100
#define DISTORTION_PERMANENT 1
#define DISTORTION_UPDATE_FREQUENCY 15
#define DISTORTION_START_DEGRADE 0.5
#define DISTORTION_END_HEIGHT 1
#define DISTORTION_EXTRAPOLATE_CORNERS 0
#define DISTORTION_XMIN 10
#define DISTORTION_YMIN 10
#define DISTORTION_XMAX 190
#define DISTORTION_YMAX 190
#define FEATURE_BABYSTEPPING 1
#define BABYSTEP_MULTIPLICATOR 1
#define DELTA_SEGMENTS_PER_SECOND_PRINT 180 // Move accurate setting for print moves
#define DELTA_SEGMENTS_PER_SECOND_MOVE 70 // Less accurate setting for other moves
#define EXACT_DELTA_MOVES 1
#define DELTA_HOME_ON_POWER 0
#define DELTASEGMENTS_PER_PRINTLINE 24
#define STEPPER_INACTIVE_TIME 360L
#define MAX_INACTIVE_TIME 0L
#define MAX_FEEDRATE_X 400
#define MAX_FEEDRATE_Y 400
#define MAX_FEEDRATE_Z 8
#define HOMING_FEEDRATE_X 40
#define HOMING_FEEDRATE_Y 40
#define HOMING_FEEDRATE_Z 4
#define HOMING_ORDER HOME_ORDER_XYZ
#define ZHOME_MIN_TEMPERATURE 0
#define ZHOME_HEAT_ALL 1
#define ZHOME_HEAT_HEIGHT 20
#define ZHOME_X_POS 999999
#define ZHOME_Y_POS 999999
#define ENABLE_BACKLASH_COMPENSATION 0
#define X_BACKLASH 0
#define Y_BACKLASH 0
#define Z_BACKLASH 0
#define RAMP_ACCELERATION 1
#define STEPPER_HIGH_DELAY 0
#define DIRECTION_DELAY 0
#define STEP_DOUBLER_FREQUENCY 12000
#define ALLOW_QUADSTEPPING 1
#define DOUBLE_STEP_DELAY 0 // time in microseconds
#define MAX_ACCELERATION_UNITS_PER_SQ_SECOND_X 1000
#define MAX_ACCELERATION_UNITS_PER_SQ_SECOND_Y 1000
#define MAX_ACCELERATION_UNITS_PER_SQ_SECOND_Z 100
#define MAX_TRAVEL_ACCELERATION_UNITS_PER_SQ_SECOND_X 1000
#define MAX_TRAVEL_ACCELERATION_UNITS_PER_SQ_SECOND_Y 1000
#define MAX_TRAVEL_ACCELERATION_UNITS_PER_SQ_SECOND_Z 100
#define INTERPOLATE_ACCELERATION_WITH_Z 0
#define ACCELERATION_FACTOR_TOP 100
#define MAX_JERK 5
#define MAX_ZJERK 0.3
#define PRINTLINE_CACHE_SIZE 16
#define MOVE_CACHE_LOW 10
#define LOW_TICKS_PER_MOVE 250000
#define EXTRUDER_SWITCH_XY_SPEED 100
#define DUAL_X_AXIS 0
#define FEATURE_TWO_XSTEPPER 0
#define X2_STEP_PIN   ORIG_E1_STEP_PIN
#define X2_DIR_PIN    ORIG_E1_DIR_PIN
#define X2_ENABLE_PIN ORIG_E1_ENABLE_PIN
#define FEATURE_TWO_YSTEPPER 0
#define Y2_STEP_PIN   ORIG_E1_STEP_PIN
#define Y2_DIR_PIN    ORIG_E1_DIR_PIN
#define Y2_ENABLE_PIN ORIG_E1_ENABLE_PIN
#define FEATURE_TWO_ZSTEPPER 0
#define Z2_STEP_PIN   ORIG_E1_STEP_PIN
#define Z2_DIR_PIN    ORIG_E1_DIR_PIN
#define Z2_ENABLE_PIN ORIG_E1_ENABLE_PIN
#define FEATURE_THREE_ZSTEPPER 0
#define Z3_STEP_PIN   ORIG_E2_STEP_PIN
#define Z3_DIR_PIN    ORIG_E2_DIR_PIN
#define Z3_ENABLE_PIN ORIG_E2_ENABLE_PIN
#define FEATURE_DITTO_PRINTING 0
#define USE_ADVANCE 0
#define ENABLE_QUADRATIC_ADVANCE 0
#define BAUDRATE 115200
#define ENABLE_POWER_ON_STARTUP 1
#define POWER_INVERTING 0
#define KILL_METHOD 1
#define ACK_WITH_LINENUMBER 1
#define WAITING_IDENTIFIER "wait"
#define ECHO_ON_EXECUTE 1
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

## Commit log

2019-05-06 Move the Bad Robin repo
    [BR-v1-Display_Holder.stl, BR-v1-Fan_Shroud.stl, BR-v1-Foot.stl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]
2019-08-14 Add Extras Dir, add missing 15mm Z-Nut STL
    [BR-v1-Z_Nut_Holder-15mm.stl, DualExtruderDriverMount.stl, Item40Plug.stl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]

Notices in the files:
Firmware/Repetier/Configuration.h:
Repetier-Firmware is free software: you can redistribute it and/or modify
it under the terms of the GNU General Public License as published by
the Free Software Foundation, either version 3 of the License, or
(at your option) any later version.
